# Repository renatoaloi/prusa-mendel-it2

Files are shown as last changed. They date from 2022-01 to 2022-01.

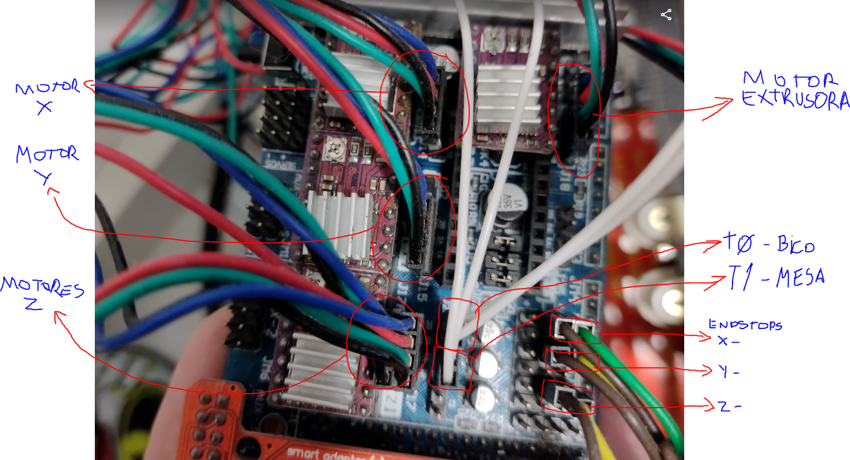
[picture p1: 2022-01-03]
imgs/EsquemaRamps1.PNG

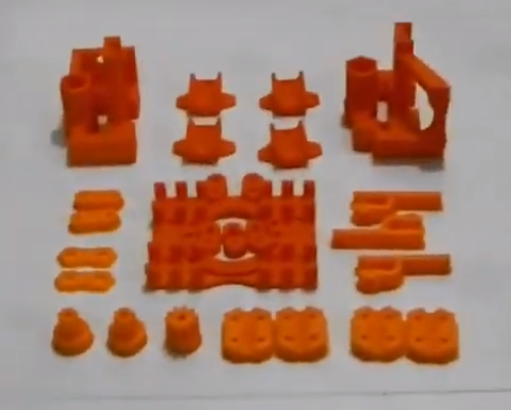
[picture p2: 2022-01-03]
imgs/peças2.png

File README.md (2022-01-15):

# prusa-mendel-it2
Repositório de arquivos da Prusa Mendel IT2 do Curso Arduino

Playlist:
https://www.youtube.com/playlist?list=PLZBvA3l7rI6FJIXnLiigdH5EZx48wwpoT

Kit Eletrônico no Mercado Livre:
https://lista.mercadolivre.com.br/kit-ramps-1.6#D[A:kit%20ramps%201.6]

Peças impressas no Mercado Livre:
https://lista.mercadolivre.com.br/kit-pe%C3%A7as-prusa-mendel-it2#D[A:kit%20pe%C3%A7as%20prusa%20mendel%20it2]

Introdução:

Videos 1 - 6

Montagem:

Videos 7 - 18

Ultimaker Cura

https://ultimaker.com/software/ultimaker-cura

https://reprap.org/wiki/Prusa_Mendel

https://reprap.org/wiki/Prusa_Mendel_(iteration_2)

https://github.com/josefprusa/PrusaMendel

https://manuais3dm.blogspot.com/p/home_20.html

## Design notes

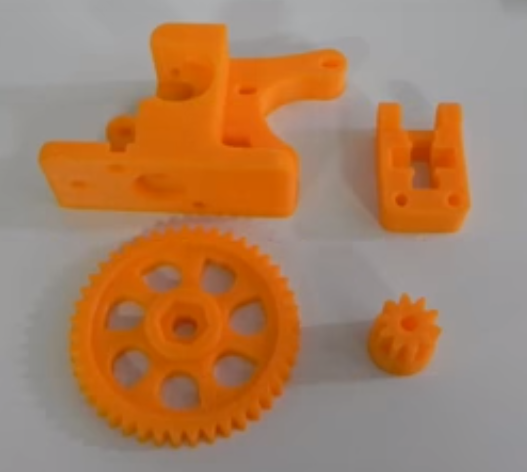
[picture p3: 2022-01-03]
imgs/peças3.png

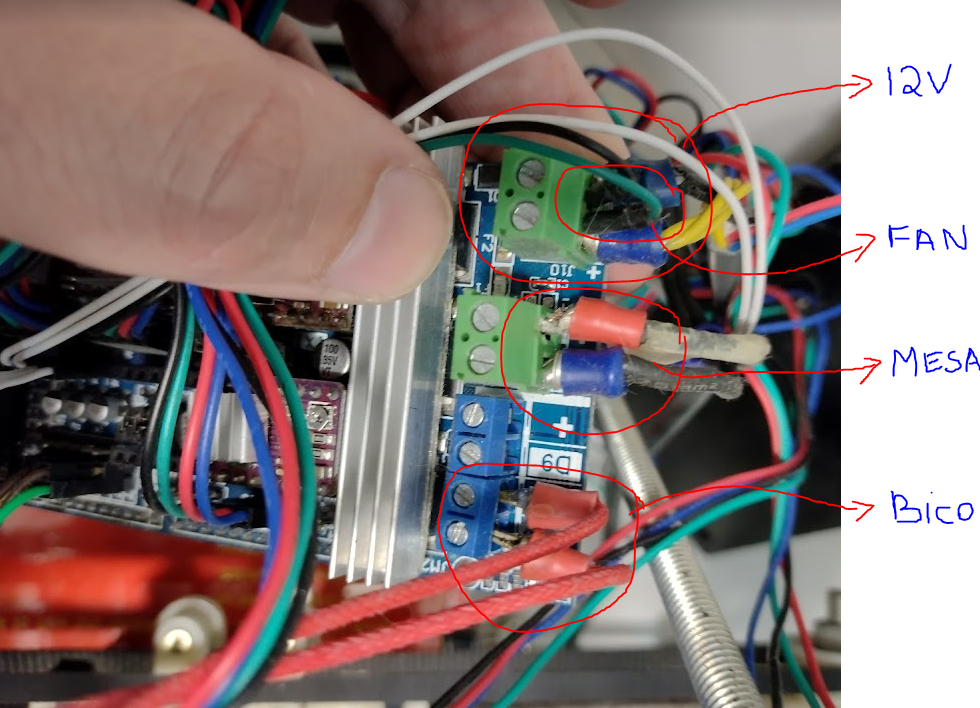
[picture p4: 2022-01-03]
imgs/EsquemaRamps2.PNG

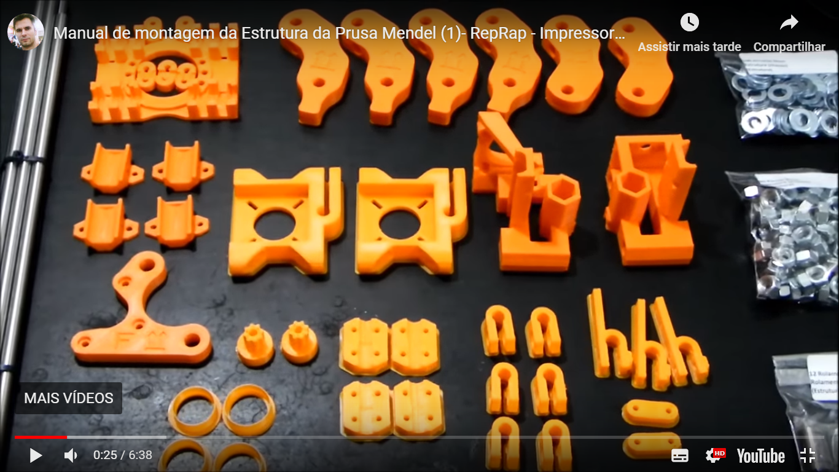
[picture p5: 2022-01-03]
imgs/peças1.png

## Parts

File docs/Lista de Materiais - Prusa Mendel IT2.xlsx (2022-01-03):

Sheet: Peças Impressas
Quantity | Description | Type | Comments | Diagram
2 | coupling | RP | stl[[1]] (https://github.com/prusajr/PrusaMendel/blob/master/metric-prusa-lm8uu/coupling.stl)
3 | endstop-holder | RP | stl[[2]] (https://github.com/prusajr/PrusaMendel/blob/master/metric-prusa-lm8uu/endstop-holder.stl)
1 | x-carriage | RP | stl[[3]] (https://github.com/prusajr/PrusaMendel/blob/master/metric-prusa-lm8uu/x-carriage.stl)
1 | x-end-idler | RP | stl[[4]] (https://github.com/prusajr/PrusaMendel/blob/master/metric-prusa-lm8uu/x-end-idler.stl)
1 | x-end-motor | RP | stl[[5]] (https://github.com/prusajr/PrusaMendel/blob/master/metric-prusa-lm8uu/x-end-motor.stl)
1 | y-motor-bracket | RP
2 | z-motor-mount | RP | stl[[6]] (https://github.com/prusajr/PrusaMendel/blob/master/metric-prusa-lm8uu/z-motor-mount.stl)
4 | belt-clamp | RP | stl[[7]] (https://github.com/prusajr/PrusaMendel/blob/master/metric-prusa-lm8uu/belt-clamp.stl)
8 | bar-clamp | RP
2 | rod-clamp | RP
2 | pulley | RP
4 | frame-vertex with foot | RP
2 | frame-vertex | RP
12 | pla-bushing | RP-PLA | check your build file, the file makes either 4 or 12

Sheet: Outras Peças
Quantity | Description | Type | Comments
83 | M8 nut | Fastener | Buy a 100-pack to be on the safe side. (https://reprap.org/wiki/File:M8nut.jpg)
93 | M8 washer | Fastener | Buy a 100-pack to be on the safe side. (Grade 2 works fine.)
6 | M8×30 mudguard / fender washer | Fastener | These are also known as penny washers, they have a much larger outer diameter than regular washers.
2 | M4×20 bolt | Fastener | To mount the extruder
2 | M4 nut | Fastener | To mount the extruder
2 | M4 washer | Fastener | To mount the extruder
22 | M3×10 bolt | Fastener
16 | M3×25 bolt | Fastener | Or eight M3×25 bolt plus eight M3x20 bolts. The M3x25 bolts are too long for the recent Prusa z-motor-holder and rod-clamp, and also for the Z motor couplings. See Section 8, steps 4 and 13 for details.
4 | M3×40 bolt | Fastener
70 | M3 washer | Fastener
40 | M3 nut | Fastener | 8 optionally locknut / stop nut / nyloc
2 | M3 grub screw / set screw | Fastener | M3x8 seems about ideal but anything 6mm or longer should do. If these are hard to get, additional M3×10 bolts will do the job instead.
3 | 608 roller skate / inline skate / skateboard bearing | Bearings | You don't need to ask for a "608 bearing" at a skate shop, just ask for wheel bearings.
4 | ballpoint pen springs | Spring | To fit over M3 bolts. Ballpoint pens are a common, cheap source of suitable springs. They are about 25mm long and compress to about 10mm.
6 | M8×370mm | Threaded rod | 3 per side Note: The threaded rods can be cut from larger 6x1m pieces (see Threaded Rod Cut Order below).
4 | M8×294mm | Threaded rod | front / rear
3 | M8×440mm | Threaded rod | top / bottom
2 | M8×210mm | Threaded rod | Z-leadscrew
1 | M8×50mm | Threaded rod | or M8x30 or longer bolt for X idler. Take care: if the bolt is too long, it may not be threaded along a sufficient length
2 | 8mm×420mm | Smooth rod | X-bar Note: 304 Stainless Steel, A2 Tool Steel, or O1 Tool Steel are recommended for smooth rods as it can help to prevent friction from rust and manufacturing (straightness) standards are higher. Rust issues can be prevented on the normal steel rods by maintaining a coat of oil. The smooth rods can also be cut from larger 3x1m pieces (see Smooth Rod Cut Order below).
2 | 8mm×406mm | Smooth rod | Y-bar
2 | 8mm×350mm | Smooth rod | Z-bar
1 | 225mm×225mm print top plate | Thick Sheet
1 | 140mm×225mm print bottom plate | Thick Sheet | Note: The Prusa Iteration 2 design does not use a print bottom plate.
1 | 840mm×5mm T5 pitch timing belt | Belt | Y axis
1 | 1380mm×5mm T5 pitch timing belt | Belt
5 | NEMA 17 bipolar stepper motor | Motor
50 | small cable binder / ziptie | Consumables | or other cable management
10 | 8mm Linear Bearings - LMU88 | Bearings

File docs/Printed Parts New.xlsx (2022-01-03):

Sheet: BOM
ID | Qtde | Part | Descrição | Opcional | Obs | Link
1 | 8 | Bar clamps | Braçadeiras de barras |  | Conectam as barras e dão suporte ao frame | https://github.com/josefprusa/PrusaMendel/blob/master/metric-prusa-lm8uu/bar-clamp.stl
2 | 2 | Bearing guide | Guias de rolamento | X | Opcional, pode ser substituído por arruelas de funileiro | https://github.com/josefprusa/PrusaMendel/blob/master/metric-prusa-lm8uu/bearing-guide.stl
3 | 4 | Belt clamp | Braçadeiras de correias |  | Usadas para prender a correia dentada na mesa do eixo Y | https://github.com/josefprusa/PrusaMendel/blob/master/metric-prusa-lm8uu/belt-clamp.stl
4 | 2 | Belt clamp nut holder | Trava de porca das braçadeiras de correias | X | Opcional, pode ser preso sem essas travas de porcas, mas facilitam o trabalho de montagem | https://github.com/josefprusa/PrusaMendel/blob/master/metric-prusa-lm8uu/belt-clamp-nut-holder.stl
5 | 2 | Coupling | Acopladores |  | Conectam os eixos dos motores do eixo Z nas barras roscadas | https://github.com/josefprusa/PrusaMendel/blob/master/metric-prusa-lm8uu/coupling.stl
6 | 3 | Endstop holder | Suporte dos sensores de fim de curso | X | Opcional, pois são peças de segurança que podem ser impressas depois quando a impressora estiver pronta | https://github.com/josefprusa/PrusaMendel/blob/master/metric-prusa-lm8uu/endstop-holder.stl
7 | 4 | Frame vertex foot | Vértice do quadro com pé |  | Conectores principais da base do quadro, com pés | https://github.com/josefprusa/PrusaMendel/blob/master/metric-prusa-lm8uu/frame-vertex-foot.stl
8 | 2 | Frame vertex | Vértice do quadro |  | Conectores principais do topo do quadro | https://github.com/josefprusa/PrusaMendel/blob/master/metric-prusa-lm8uu/frame-vertex.stl
9 | 2 | Pulley | Polias |  | Pinhão do motor | https://github.com/josefprusa/PrusaMendel/blob/master/metric-prusa-lm8uu/pulley.stl
10 | 2 | Rod clamp | Braçadeiras das barras lisas |  | Braçadeiras do mancal do eixo Z | https://github.com/josefprusa/PrusaMendel/blob/master/metric-prusa-lm8uu/rod-clamp.stl
11 | 1 | Wade big | Tracionador grande |  | Engrenagem grande de tração do extrusor | https://github.com/josefprusa/PrusaMendel/blob/master/metric-prusa-lm8uu/wade-big.stl
12 | 1 | Wade small | Tracionador pequeno |  | Engrenagem pequena de tração do extrusor | https://github.com/josefprusa/PrusaMendel/blob/master/metric-prusa-lm8uu/wade-small.stl
13 | 1 | Wade | Tracionador |  | Corpo do tracionador do extrusor | https://github.com/josefprusa/PrusaMendel/blob/master/metric-prusa-lm8uu/wade.stl
14 | 1 | X carriage | Carro X |  | Carro do eixo X | https://github.com/josefprusa/PrusaMendel/blob/master/metric-prusa-lm8uu/x-carriage.stl
15 | 1 | X end idler | Terminador X (R) |  | Terminal direito do eixo X | https://github.com/josefprusa/PrusaMendel/blob/master/metric-prusa-lm8uu/x-end-idler.stl
16 | 1 | X end motor | Terminador do motor X (L) |  | Terminal do motor (lado esquerdo) do eixo X | https://github.com/josefprusa/PrusaMendel/blob/master/metric-prusa-lm8uu/x-end-motor.stl
17 | 3 | Y bushing | Buchas Y |  | Buchas da mesa do eixo Y | https://github.com/josefprusa/PrusaMendel/blob/master/metric-prusa-lm8uu/y-bushing.stl
18 | 1 | Y bracket | Suporte T do eixo Y |  | Suporte do motor do eixo Y em forma de "T" | https://github.com/josefprusa/PrusaMendel/blob/master/metric-prusa-lm8uu/ybrac-t.stl
19 | 2 | Z motor mount | Mancal do motor Z |  | Suporte do motor do eixo Z | https://github.com/josefprusa/PrusaMendel/blob/master/metric-prusa-lm8uu/z-motor-mount.stl

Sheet: Plates
Plate | Link | Parts
1 | https://github.com/josefprusa/PrusaMendel/blob/master/metric-prusa-lm8uu/mendel-plate-1.stl | 15, 16, 13, 6, 1 (2/8)
2 | https://github.com/josefprusa/PrusaMendel/blob/master/metric-prusa-lm8uu/mendel-plate-2.stl | 7, 8
3 | https://github.com/josefprusa/PrusaMendel/blob/master/metric-prusa-lm8uu/mendel-plate-3.stl | 1 (6/8), 19, 5, 18, 11
4 | https://github.com/josefprusa/PrusaMendel/blob/master/metric-prusa-lm8uu/mendel-plate-4.stl | 2, 17, 14, 10, 3, 4, 12
Pinhão do motor | https://github.com/josefprusa/PrusaMendel/blob/master/metric-prusa-lm8uu/pulley.stl | 9 x 2

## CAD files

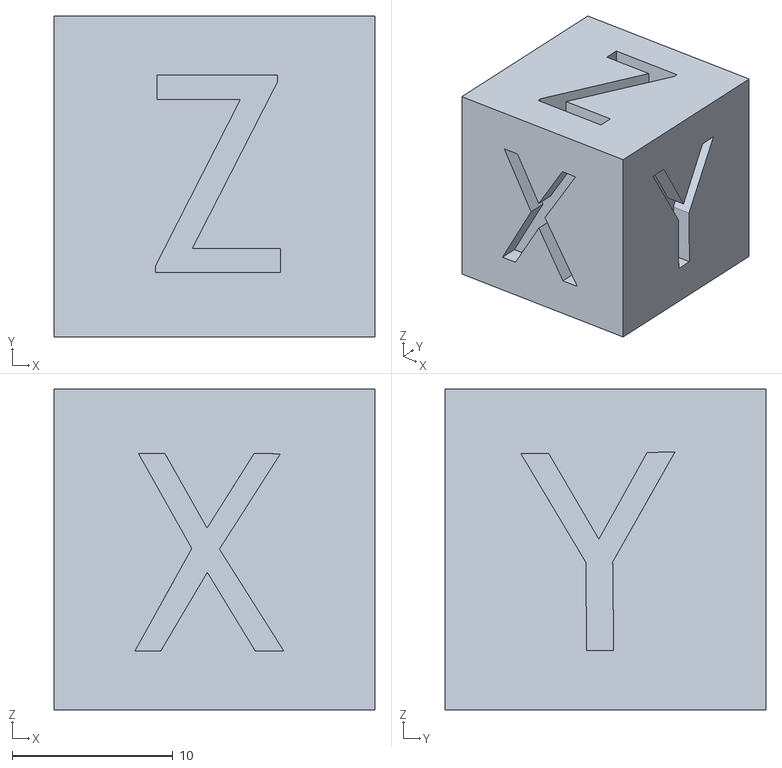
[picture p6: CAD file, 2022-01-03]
xyzCalibration_cube.stl
20.0 x 20.0 x 20.0

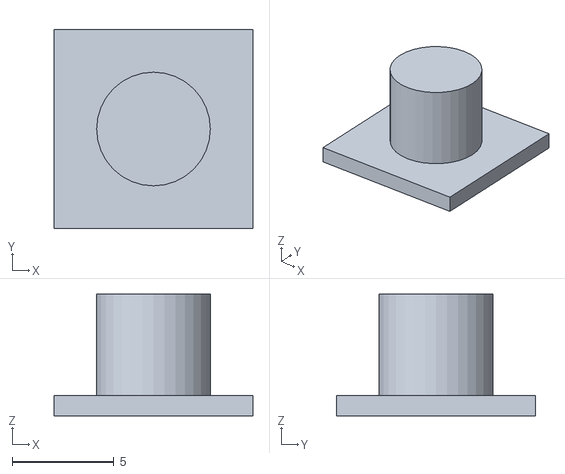
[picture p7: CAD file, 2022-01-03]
smartlcd_button.stl
9.80 x 9.80 x 6.00

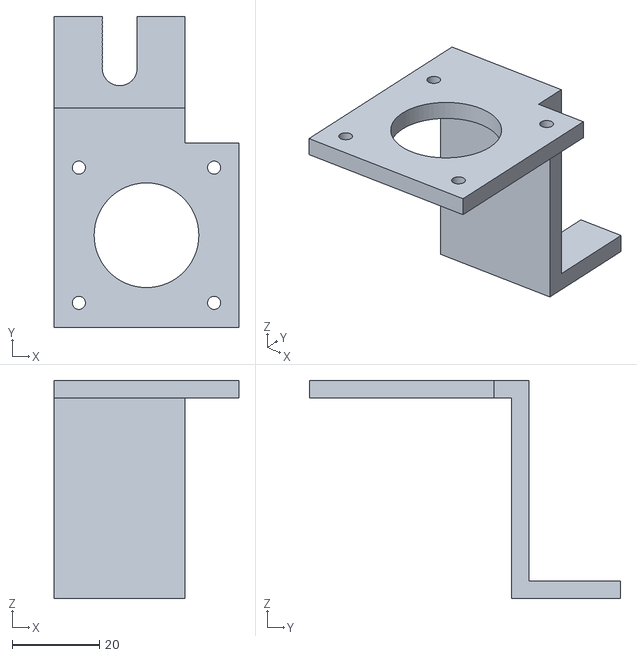
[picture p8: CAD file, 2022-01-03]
MotorMount2.stl
42.3 x 71.3 x 50.0

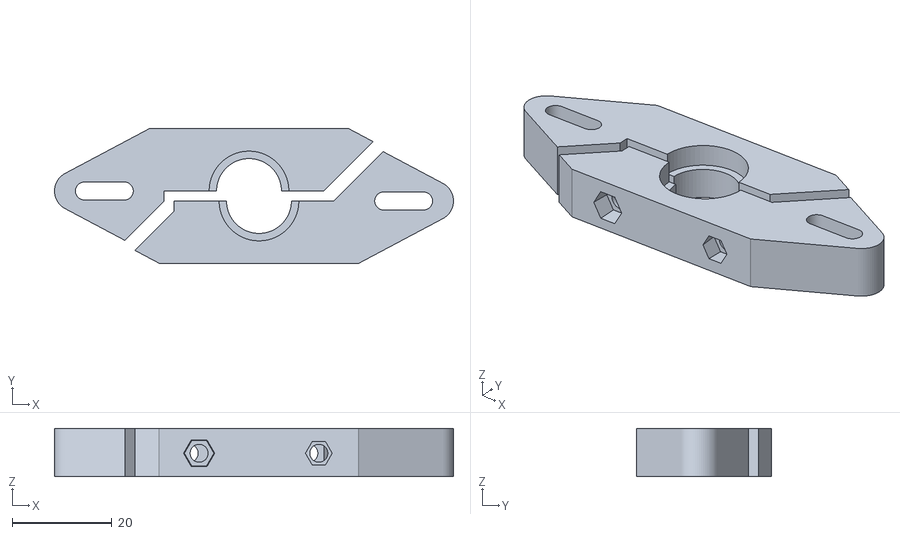
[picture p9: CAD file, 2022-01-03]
GrooveMount_Parametric.stl
80.0 x 27.0 x 9.70

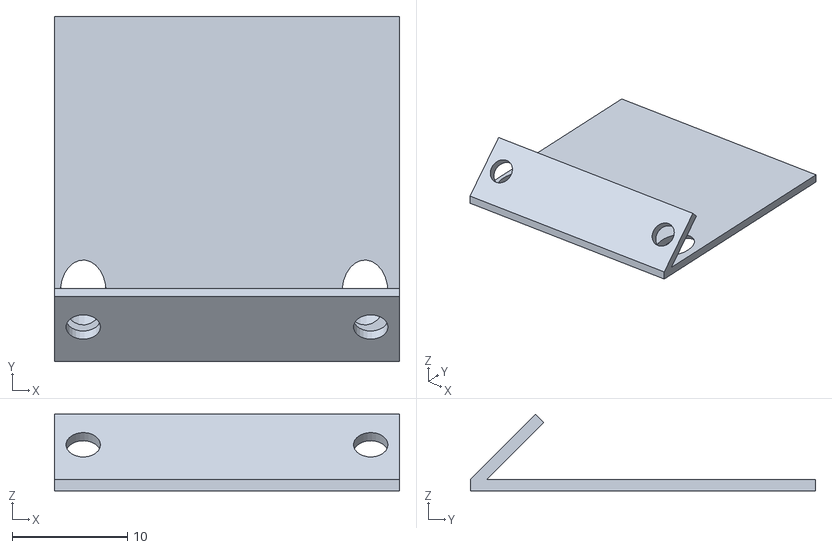
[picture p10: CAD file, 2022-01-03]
fan_deflector.stl
30.0 x 30.0 x 6.66

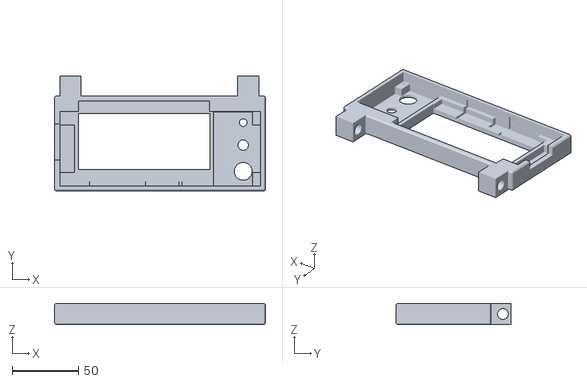
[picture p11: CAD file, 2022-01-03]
smartlcd2.stl
159.0 x 86.5 x 16.0

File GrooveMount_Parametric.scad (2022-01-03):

$fn=60;

inner_radius = 12;
slack = 1;
i = (inner_radius + slack) / 2;

outer_radius = 16;
o = outer_radius / 2;

// h = 4.8; // Prusa 
hight = 6;
h = hight - 0.3;


centerdistance = 50;
cd = centerdistance;

s = 1;

module head()
{
	cylinder(h,i,i);
	translate([0,0,h])  cylinder(5,o,o);
	translate([0,0,-h]) cylinder(h,o,o);
}

module block()
{
	hull()
	{
		translate([0,0,h/2])	 		cube([40,25,h],true);
		translate([0,0,-2])   		cube([40,25,4],true);

		translate([10+cd/2,0,-4]) 	cylinder(h+4,4,4);
		translate([-10-cd/2,0,-4]) 	cylinder(h+4,4,4);
	}
}

module plate()
{
	difference()
	{
		block();
		head();

		hull()
		{
			translate([ cd/2,0,-10]) cylinder(30,1.8,1.8);
			translate([ 8+cd/2,0,-10]) cylinder(30,1.8,1.8);
		}

		hull()
		{
			translate([-cd/2,0,-10]) cylinder(30,1.8,1.8);
			translate([-8-cd/2,0,-10]) cylinder(30,1.8,1.8);
		}

		translate([ 12,25,s]) rotate([90,0,0]) cylinder(50,1.8,1.8);
		translate([-12,25,s]) rotate([90,0,0]) cylinder(50,1.8,1.8);
		
		sinks();
	}
}

module sinks()
{
	translate([-12,14,s]) rotate([90,0,0]) cylinder(4,5.4/2, 5.4/2);
	translate([ 12,14,s]) rotate([90,0,0]) cylinder(4,5.4/2, 5.4/2);

	translate([-12,-9,s]) rotate([90,0,0]) cylinder(4,5.9/2, 5.3/2, $fn=6);
	translate([ 12,-9,s]) rotate([90,0,0]) cylinder(4,5.9/2, 6.3/2, $fn=6);
}


module cl() 
{ 
	translate([-15,0,0]) rotate([0,0,0]) cut(); 
}

module dr() 
{ 
	mirror([1,0,0]) mirror([0,1,0]) translate([-15,0,0]) rotate([0,00,0]) cut(); 
}

module oneplate()
{
	difference()
	{
		plate();
		cl();
	
		translate([-15,0,-10]) cube([70,30,20]);
		translate([17,-15,-10]) cube([30,30,20]);		
	}

	intersection()
	{
		plate();
		dr();
	}

}

module cut()
{
	translate([0,0,-10])
	difference()
	{
		rotate([0,0,45]) 		  cube([26,26,20]);
		translate([0,0,0])     cube([40,40,20]);
	}
}


rotate([0,180,0])
{
	difference()
	{
		plate();
		oneplate();
	}
}

translate([2,-2,0]) rotate([0,180,0]) oneplate();

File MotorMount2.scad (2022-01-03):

$fn=64;
md = 42.3;
w=4;
f=1.5;
shaft=12;

difference() {
    
    cube([md, md, w]);
    
    translate([md/2-15.5, md/2-15.5, -3])
    cylinder(r=f, h=10);

    translate([md/2+15.5, md/2-15.5, -3])
    cylinder(r=f, h=10);

    translate([md/2+15.5, md/2+15.5, -3])
    cylinder(r=f, h=10);

    translate([md/2-15.5, md/2+15.5, -3])
    cylinder(r=f, h=10);
    
    // furo do shaft
    translate([md/2, md/2, -3])
    cylinder(r=shaft, h=10);


}

translate([0, md, 0])
cube([30, w, w]);

translate([0, md+w, w-50])
cube([30, w, 50]);

translate([30, md+w, w-50])
rotate([-90,180,0])
hook();

//translate([md/2-15, -39, 0])
//cube([30, 40, w]);

module hook() {
    difference() {
        cube([30, w, 25]);

        rotate([90,0,0])
        translate([30/2, md/2+3, -7])
        cylinder(r=4, h=10);
        rotate([90,0,0])
        translate([30/2, md/2+2, -7])
        cylinder(r=4, h=10);
        rotate([90,0,0])
        translate([30/2, md/2+1, -7])
        cylinder(r=4, h=10);
        rotate([90,0,0])
        translate([30/2, md/2, -7])
        cylinder(r=4, h=10);
        rotate([90,0,0])
        translate([30/2, md/2-1, -7])
        cylinder(r=4, h=10);
        rotate([90,0,0])
        translate([30/2, md/2-2, -7])
        cylinder(r=4, h=10);
        rotate([90,0,0])
        translate([30/2, md/2-3, -7])
        cylinder(r=4, h=10);
        rotate([90,0,0])
        translate([30/2, md/2-4, -7])
        cylinder(r=4, h=10);
        rotate([90,0,0])
        translate([30/2, md/2-5, -7])
        cylinder(r=4, h=10);
        rotate([90,0,0])
        translate([30/2, md/2-6, -7])
        cylinder(r=4, h=10);
        rotate([90,0,0])
        translate([30/2, md/2-7, -7])
        cylinder(r=4, h=10);
        rotate([90,0,0])
        translate([30/2, md/2-8, -7])
        cylinder(r=4, h=10);
    }
}

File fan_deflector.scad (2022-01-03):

$fn=25;

hole_left = 2.5;
hole_dia  = 1.5;
screwdriver_dia = 2;

module deflector() {
    difference() {
        // deflector wall
        cube([30,30,1]);

        // holes for screwdriver
        translate([hole_left,4,3])
        rotate(a=225, v=[1,0,0])
        cylinder(r=screwdriver_dia, h=10);

        translate([screwdriver_dia+25,4,3])
        rotate(a=225, v=[1,0,0])
        cylinder(r=screwdriver_dia, h=10);
    }
}

module mount() {
    difference() {

        // wall for mount
        translate([0,0,1])
        rotate(a=-45, v=[1,0,0])
        cube([30,1,8]);

        // holes for fixation
        translate([hole_left,4,3])
            rotate(a=45, v=[1,0,0])
        cylinder(r=hole_dia, h=10);

        translate([hole_left+25,4,3])
            rotate(a=45, v=[1,0,0])
        cylinder(r=hole_dia, h=10);

    }
}

deflector();
mount();

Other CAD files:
smartlcd2.scad
smartlcd_button.scad

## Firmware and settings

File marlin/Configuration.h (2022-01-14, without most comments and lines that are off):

#pragma once
#define CONFIGURATION_H_VERSION 02000903
#define STRING_CONFIG_H_AUTHOR "Renato Aloi" // Who made the changes.
#define SHOW_BOOTSCREEN
  #define MOTHERBOARD BOARD_RAMPS_14_EFB
#define SERIAL_PORT 0
#define BAUDRATE 250000
#define CUSTOM_MACHINE_NAME "Aloi3D"
#define MACHINE_UUID "aaabb63c-e030-4cd7-b527-b6270485dd69"
#if LINEAR_AXES >= 4
  #define AXIS4_NAME 'A' // :['A', 'B', 'C', 'U', 'V', 'W']
#endif
#if LINEAR_AXES >= 5
  #define AXIS5_NAME 'B' // :['A', 'B', 'C', 'U', 'V', 'W']
#endif
#if LINEAR_AXES >= 6
  #define AXIS6_NAME 'C' // :['A', 'B', 'C', 'U', 'V', 'W']
#endif
#define EXTRUDERS 1
#define DEFAULT_NOMINAL_FILAMENT_DIA 1.75
#define TEMP_SENSOR_0 5
#define TEMP_SENSOR_1 0
#define TEMP_SENSOR_2 0
#define TEMP_SENSOR_3 0
#define TEMP_SENSOR_4 0
#define TEMP_SENSOR_5 0
#define TEMP_SENSOR_6 0
#define TEMP_SENSOR_7 0
#define TEMP_SENSOR_BED 11
#define TEMP_SENSOR_PROBE 0
#define TEMP_SENSOR_CHAMBER 0
#define TEMP_SENSOR_COOLER 0
#define TEMP_SENSOR_BOARD 0
#define TEMP_SENSOR_REDUNDANT 0
#define DUMMY_THERMISTOR_998_VALUE  25
#define DUMMY_THERMISTOR_999_VALUE 100
#define TEMP_RESIDENCY_TIME         10  // (seconds) Time to wait for hotend to "settle" in M109
#define TEMP_WINDOW                  1  // (°C) Temperature proximity for the "temperature reached" timer
#define TEMP_HYSTERESIS              3  // (°C) Temperature proximity considered "close enough" to the target
#define TEMP_BED_RESIDENCY_TIME     10  // (seconds) Time to wait for bed to "settle" in M190
#define TEMP_BED_WINDOW              1  // (°C) Temperature proximity for the "temperature reached" timer
#define TEMP_BED_HYSTERESIS          3  // (°C) Temperature proximity considered "close enough" to the target
#define TEMP_CHAMBER_RESIDENCY_TIME 10  // (seconds) Time to wait for chamber to "settle" in M191
#define TEMP_CHAMBER_WINDOW          1  // (°C) Temperature proximity for the "temperature reached" timer
#define TEMP_CHAMBER_HYSTERESIS      3  // (°C) Temperature proximity considered "close enough" to the target
#if TEMP_SENSOR_REDUNDANT
  #define TEMP_SENSOR_REDUNDANT_SOURCE    E1  // The sensor that will provide the redundant reading.
  #define TEMP_SENSOR_REDUNDANT_TARGET    E0  // The sensor that we are providing a redundant reading for.
  #define TEMP_SENSOR_REDUNDANT_MAX_DIFF  10  // (°C) Temperature difference that will trigger a print abort.
#endif
#define HEATER_0_MINTEMP   5
#define HEATER_1_MINTEMP   5
#define HEATER_2_MINTEMP   5
#define HEATER_3_MINTEMP   5
#define HEATER_4_MINTEMP   5
#define HEATER_5_MINTEMP   5
#define HEATER_6_MINTEMP   5
#define HEATER_7_MINTEMP   5
#define BED_MINTEMP        5
#define CHAMBER_MINTEMP    5
#define HEATER_0_MAXTEMP 275
#define HEATER_1_MAXTEMP 275
#define HEATER_2_MAXTEMP 275
#define HEATER_3_MAXTEMP 275
#define HEATER_4_MAXTEMP 275
#define HEATER_5_MAXTEMP 275
#define HEATER_6_MAXTEMP 275
#define HEATER_7_MAXTEMP 275
#define BED_MAXTEMP      150
#define CHAMBER_MAXTEMP  60
#define HOTEND_OVERSHOOT 15   // (°C) Forbid temperatures over MAXTEMP - OVERSHOOT
#define BED_OVERSHOOT    10   // (°C) Forbid temperatures over MAXTEMP - OVERSHOOT
#define COOLER_OVERSHOOT  2   // (°C) Forbid temperatures closer than OVERSHOOT
#define BANG_MAX 255     // Limits current to nozzle while in bang-bang mode; 255=full current
#define PID_MAX BANG_MAX // Limits current to nozzle while PID is active (see PID_FUNCTIONAL_RANGE below); 255=full current
#define PID_K1 0.95      // Smoothing factor within any PID loop
#define MAX_BED_POWER 255 // limits duty cycle to bed; 255=full current
#define MAX_CHAMBER_POWER 255 // limits duty cycle to chamber heater; 255=full current
#define PREVENT_COLD_EXTRUSION
#define EXTRUDE_MINTEMP 170
#define PREVENT_LENGTHY_EXTRUDE
#define EXTRUDE_MAXLENGTH 200
#define THERMAL_PROTECTION_HOTENDS // Enable thermal protection for all extruders
#define THERMAL_PROTECTION_BED     // Enable thermal protection for the heated bed
#define THERMAL_PROTECTION_CHAMBER // Enable thermal protection for the heated chamber
#define THERMAL_PROTECTION_COOLER  // Enable thermal protection for the laser cooling
#define USE_XMIN_PLUG
#define USE_YMIN_PLUG
#define USE_ZMIN_PLUG
#define ENDSTOPPULLUPS
#define X_MIN_ENDSTOP_INVERTING true // Set to true to invert the logic of the endstop.
#define Y_MIN_ENDSTOP_INVERTING true // Set to true to invert the logic of the endstop.
#define Z_MIN_ENDSTOP_INVERTING true // Set to true to invert the logic of the endstop.
#define I_MIN_ENDSTOP_INVERTING false // Set to true to invert the logic of the endstop.
#define J_MIN_ENDSTOP_INVERTING false // Set to true to invert the logic of the endstop.
#define K_MIN_ENDSTOP_INVERTING false // Set to true to invert the logic of the endstop.
#define X_MAX_ENDSTOP_INVERTING false // Set to true to invert the logic of the endstop.
#define Y_MAX_ENDSTOP_INVERTING false // Set to true to invert the logic of the endstop.
#define Z_MAX_ENDSTOP_INVERTING false // Set to true to invert the logic of the endstop.
#define I_MAX_ENDSTOP_INVERTING false // Set to true to invert the logic of the endstop.
#define J_MAX_ENDSTOP_INVERTING false // Set to true to invert the logic of the endstop.
#define K_MAX_ENDSTOP_INVERTING false // Set to true to invert the logic of the endstop.
#define Z_MIN_PROBE_ENDSTOP_INVERTING false // Set to true to invert the logic of the probe.
#define X_DRIVER_TYPE  DRV8825
#define Y_DRIVER_TYPE  DRV8825
#define Z_DRIVER_TYPE  DRV8825
#define E0_DRIVER_TYPE DRV8825
#define DEFAULT_AXIS_STEPS_PER_UNIT   { 160, 160, 5120, 209.3f }
#define DEFAULT_MAX_FEEDRATE          { 300, 300, 5, 25 }
#define DEFAULT_MAX_ACCELERATION      { 3000, 3000, 100, 10000 }
#define DEFAULT_ACCELERATION          3000    // X, Y, Z and E acceleration for printing moves
#define DEFAULT_RETRACT_ACCELERATION  3000    // E acceleration for retracts
#define DEFAULT_TRAVEL_ACCELERATION   3000    // X, Y, Z acceleration for travel (non printing) moves
#define DEFAULT_EJERK    5.0  // May be used by Linear Advance
  #define JUNCTION_DEVIATION_MM 0.013 // (mm) Distance from real junction edge
  #define JD_HANDLE_SMALL_SEGMENTS    // Use curvature estimation instead of just the junction angle
#define Z_MIN_PROBE_USES_Z_MIN_ENDSTOP_PIN
#define NOZZLE_TO_PROBE_OFFSET { 10, 10, 0 }
#define PROBING_MARGIN 10
#define XY_PROBE_FEEDRATE (133*60)
#define Z_PROBE_FEEDRATE_FAST (4*60)
#define Z_PROBE_FEEDRATE_SLOW (Z_PROBE_FEEDRATE_FAST / 2)
#define Z_CLEARANCE_DEPLOY_PROBE   10 // Z Clearance for Deploy/Stow
#define Z_CLEARANCE_BETWEEN_PROBES  5 // Z Clearance between probe points
#define Z_CLEARANCE_MULTI_PROBE     5 // Z Clearance between multiple probes
#define Z_PROBE_LOW_POINT          -2 // Farthest distance below the trigger-point to go before stopping
#define Z_PROBE_OFFSET_RANGE_MIN -20
#define Z_PROBE_OFFSET_RANGE_MAX 20
#define X_ENABLE_ON 0
#define Y_ENABLE_ON 0
#define Z_ENABLE_ON 0
#define E_ENABLE_ON 0 // For all extruders
#define DISABLE_X false
#define DISABLE_Y false
#define DISABLE_Z false
#define DISABLE_E false             // Disable the extruder when not stepping
#define DISABLE_INACTIVE_EXTRUDER   // Keep only the active extruder enabled
#define INVERT_X_DIR false
#define INVERT_Y_DIR true
#define INVERT_Z_DIR false
#define INVERT_E0_DIR false
#define INVERT_E1_DIR false
#define INVERT_E2_DIR false
#define INVERT_E3_DIR false
#define INVERT_E4_DIR false
#define INVERT_E5_DIR false
#define INVERT_E6_DIR false
#define INVERT_E7_DIR false
#define X_HOME_DIR -1
#define Y_HOME_DIR -1
#define Z_HOME_DIR -1
#define X_BED_SIZE 200
#define Y_BED_SIZE 200
#define X_MIN_POS 0
#define Y_MIN_POS 0
#define Z_MIN_POS 0
#define X_MAX_POS X_BED_SIZE
#define Y_MAX_POS Y_BED_SIZE
#define Z_MAX_POS 200
#define MIN_SOFTWARE_ENDSTOPS
  #define MIN_SOFTWARE_ENDSTOP_X
  #define MIN_SOFTWARE_ENDSTOP_Y
  #define MIN_SOFTWARE_ENDSTOP_Z
  #define MIN_SOFTWARE_ENDSTOP_I
  #define MIN_SOFTWARE_ENDSTOP_J
  #define MIN_SOFTWARE_ENDSTOP_K
#define MAX_SOFTWARE_ENDSTOPS
  #define MAX_SOFTWARE_ENDSTOP_X
  #define MAX_SOFTWARE_ENDSTOP_Y
  #define MAX_SOFTWARE_ENDSTOP_Z
  #define MAX_SOFTWARE_ENDSTOP_I
  #define MAX_SOFTWARE_ENDSTOP_J
  #define MAX_SOFTWARE_ENDSTOP_K
#define HOMING_FEEDRATE_MM_M { (50*60), (50*60), (4*60) }
#define VALIDATE_HOMING_ENDSTOPS
#define EEPROM_CHITCHAT       // Give feedback on EEPROM commands. Disable to save PROGMEM.
#define EEPROM_BOOT_SILENT    // Keep M503 quiet and only give errors during first load
#define HOST_KEEPALIVE_FEATURE        // Disable this if your host doesn't like keepalive messages
#define DEFAULT_KEEPALIVE_INTERVAL 2  // Number of seconds between "busy" messages. Set with M113.
#define BUSY_WHILE_HEATING            // Some hosts require "busy" messages even during heating
#define PREHEAT_1_LABEL       "PLA"
#define PREHEAT_1_TEMP_HOTEND 180
#define PREHEAT_1_TEMP_BED     70
#define PREHEAT_1_TEMP_CHAMBER 35
#define PREHEAT_1_FAN_SPEED     0 // Value from 0 to 255
#define PREHEAT_2_LABEL       "ABS"
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

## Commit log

2022-01-03 commit inicial
    [Configuration.h, GrooveMount_Parametric.scad, GrooveMount_Parametric.stl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]
2022-01-03 marlin config
    [Configuration.h, Configuration_adv.h]
2022-01-14 Marlin original config file
    [Configuration.h]
2022-01-14 ajustes config marlin
    [Configuration.h]
2022-01-14 config adv marlin original
    [Configuration_adv.h]
2022-01-14 não precisa de config adv
    [Configuration_adv.h]

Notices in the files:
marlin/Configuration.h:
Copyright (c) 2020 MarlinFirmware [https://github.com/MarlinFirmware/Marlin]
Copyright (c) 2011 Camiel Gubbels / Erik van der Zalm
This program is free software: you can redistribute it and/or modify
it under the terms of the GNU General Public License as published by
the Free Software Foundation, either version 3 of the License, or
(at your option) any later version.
